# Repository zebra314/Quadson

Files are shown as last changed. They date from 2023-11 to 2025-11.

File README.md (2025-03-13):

# Quadson

## Description

## Usage

### Simulation

- Run the simulation

  ```sh
  make
  ```

- Use docker for simulation

  ```sh
  make SIM_METHOD=docker
  ```

### Real time control on Raspberry Pi

- Activate the robot

  ```sh
  make nav
  ```

- Clean the project

  ```sh
  make nav-clean
  ```

## Files

```sh
quadson_pi/
│
├── build/
│ ├── ...
│ .
│ .
│ .
│ └──
│
├── include/
│ ├── actuator.h
│ ├── AHRS.h
│ ├── can_interface.h
│ ├── can_protocol.h
│ ├── leg_group.h
│ ├── quadson.h
│ └── utility.h
│
├── library/
│ ├── ...
│ .
│ .
│ .
│ └──
│
├── source/
│ ├── actuator.cpp
│ ├── AHRS.cpp
│ ├── can_interface.cpp
│ ├── can_protocol.cpp
│ ├── leg_group.cpp
│ ├── main.cpp
│ └── quadson.cpp
│
├── python_scripts/
│ ├── CAN_MotorControl.py
│ └── quad_calc_test.py
│
├── start_can.sh
│
└── stop_can.sh
```

- `actuator.h/actuator.cpp`: Define the basic function for a single actuator, such as enable, disable, set angle, set omega, get information, etc.

- `AHRS.h/AHRS.cpp`: Define the basic function and algorithm for the Attitude and Heading Reference System (AHRS) module. It is used to get the orientation of the robot.

- `main.cpp`: Main file of the project

- `can_interface.h/can_interface.cpp`: Create a can interface class to communicate with the can bus from the computer to the robot.

  ```sh
  Actuator alpha ─┐
  Actuator beta  ───> CAN BUS <───> Raspberry Pi
  Actuator gamma ─┘
  ```

- `can_protocol.h/can_protocol.cpp`: Define the protocol to communicate with the can bus. It includes the message ID(standard or extended), the message type, the message data, etc.

- `leg_group.h/leg_group.cpp`: Define the leg group class to control the leg group of the robot. It unified three actuators and responsible for the inverse kinematics, forward kinematics, gait planning and pid control.

- `quadson.h/quadson.cpp`: Define the main class of the project. It includes the main loop of the robot, the initialization of the robot, it also unified the four leg groups and responsible for sending the command to the actuators via the can bus.

- `utility.h`: Define some utility functions

- `start_can.sh`: Bash script to start the can interface

- `stop_can.sh`: Bash script to stop the can interface

## References

- [Mahony AHRS algorithm implemented by Madgwick](http://x-io.co.uk/open-source-imu-and-ahrs-algorithms/)

  According to the Mahony AHRS algorithm implemented by Madgwick and adapted by Igor Vereninov, provided by Emlid Ltd (c) 2014:

  ```bibtex
  @MISC{madgwick2014,
  author =   {Madgwick, S. and Vereninov, I.},
  title =    {Mahony AHRS algorithm},
  howpublished = {\url{http://x-io.co.uk/open-source-imu-and-ahrs-algorithms/}},
  year = {2014}
  }
  ```

- [PyBullet](http://pybullet.org)

  ```bibtex
  @MISC{coumans2021,
  author =   {Erwin Coumans and Yunfei Bai},
  title =    {PyBullet, a Python module for physics simulation for games, robotics and machine learning},
  howpublished = {\url{http://pybullet.org}},
  year = {2016--2021}
  }
  ```

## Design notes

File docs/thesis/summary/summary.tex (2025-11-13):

\documentclass[a4paper,11pt]{article}
\usepackage[a4paper, margin=2.5cm]{geometry}
\usepackage[utf8]{inputenc}
\usepackage{graphicx}
\usepackage{caption}
\usepackage{subcaption}
\usepackage{float}
\usepackage{amsmath}
\usepackage{pgfplots}
\usepackage{ffcode}
\usepackage{booktabs}
\usepackage{xcolor}
\usepackage{listings}
\usepackage{array}
\usepackage{tikz}
\usepackage{algorithm}
\usepackage{algpseudocode}
\usetikzlibrary{calc,patterns,angles,quotes}

\pgfplotsset{compat=1.18} 

\makeatletter
\newenvironment{breakablealgorithm}
{% \begin{breakablealgorithm}
\begin{center} %
\refstepcounter{algorithm}% New algorithm
%\hrule height.8pt depth0pt \kern2pt% \@fs@pre for \@fs@ruled
\hrule height.8pt depth0pt \kern2pt% \@fs@pre for \@fs@ruled
\renewcommand{\caption}[2][\relax]{% Make a new \caption
{\raggedright\textbf{\ALG@name~\thealgorithm} ##2\par}
\ifx\relax##1\relax
\addcontentsline{loa}{algorithm}{\protect\numberline{\thealgorithm}##2}%
\else
\addcontentsline{loa}{algorithm}{\protect\numberline{\thealgorithm}##1}%
\fi
\kern2pt\hrule\kern2pt
}
}{% \end{breakablealgorithm}
\kern2pt\hrule\relax% \@fs@post for \@fs@ruled
\end{center} %
}
\makeatother

\begin{document}
	
\title{
	\textbf{Quadson: A Quadruped Robot Control Framework}
}
\author{Ying Pei Lin}
\date{Spring 2025}
\maketitle

\section{Introduction}

Quadson is a 3D printed quadruped robot designed as a platform for exploring advanced robotic motion and control.
This document includes its forward kinematics, inverse kinematics, differential kinematics and expands to body kinematics and locomotion.
Following the analysis, we will introduce the process of performing simultion in Pybullet and using deep
reinforcement learning to improve the robot's control and performance.

\section{Forward Kinematics}

For each leg of the robot, we define the reference frame with its origin at point $p_1$. 
Two motors are positioned at $p_1$ and $p_5$ respectively, and the third motor
connected to the entire leg assembly, controls the rotation around x axis. The remaining joints in the leg are all passive.

\begin{center}
\begin{tikzpicture}[scale=0.4]
	% Points
	\coordinate (p1) at (0,0);
	\coordinate (p2) at (-5.66,-5.66);
	\coordinate (p2_hori) at (-1.66,-5.66);
	\coordinate (p3) at (2.31,-11.70);
	\coordinate (pe) at (8.68,-16.54);
	\coordinate (p4) at (13.82,-5.66);
	\coordinate (p4_hori) at (17.82,-5.66);
	\coordinate (p5) at (8.16,0);
	\coordinate (p5_hori) at (12.16,0);

	% Lines
	\draw[thick] (p1) -- (p2) -- (p3) -- (p4) -- (p5) -- (p1);
	\draw[thick] (p3) -- (pe);
	\draw[dashed] (p2) -- (p2_hori);
	\draw[dashed] (p4) -- (p4_hori);
	\draw[dashed] (p5) -- (p5_hori);
	
	% Axis
	\draw[thick,->] (-5,0,0) -- (-3,0,0) node[right] {$x$};
	\draw[thick,->] (-5,0,0) -- (-5,2,0) node[above] {$y$};
	\draw[thick,->] (-5,0,0) -- (-5,0,2) node[left] {$z$};
	\draw[red,->] (-3.8,-0.2,-0.7) arc[start angle=0,end angle=270,radius=0.5cm] node[midway,above] {$\theta_0$};

	% Point tags
	\foreach \p in {p1, p2, pe, p4, p5} {
			\fill[black] (\p) circle (4pt);
			\node[above] at (\p) {\p};
	}
	\fill[black] (p3) circle (4pt);
	\node[below] at (p3) {p3};

	% Length tags
	\draw[blue, dashed] (p1) -- (p5) node[midway, above] {$L_{0}$};
	\draw[blue, dashed] (p1) -- (p2) node[midway, above] {$L_{1}$};
	\draw[blue, dashed] (p2) -- (p3) node[midway, below] {$L_{2}$};
	\draw[blue, dashed] (p3) -- (pe) node[midway, below] {$L_{3}$};
	\draw[blue, dashed] (p3) -- (p4) node[midway, below] {$L_{4}$};
	\draw[blue, dashed] (p4) -- (p5) node[midway, below] {$L_{5}$};

	% Angle tags
	\pic [draw=red, text=red, <-, "$\theta_1$", angle radius=0.7cm] {angle=p2--p1--p5};
	\pic [draw=red, text=red, <-, "$\theta_2$", angle radius=1.2cm] {angle=p3--p2--p2_hori};
	\pic [draw=red, text=red, <-, "$\theta_4$", angle radius=0.7cm] {angle=p3--p4--p4_hori};
	\pic [draw=red, text=red, <-, "$\theta_5$", angle radius=1cm] {angle=p4--p5--p5_hori};
\end{tikzpicture}
\end{center}

The following algorithm takes the angle of three motors as input and computes the position of the end-effector.

\begin{breakablealgorithm}
	\caption{Compute Leg End-Point}
	\begin{algorithmic}[1]
			\Require Motor angles $\theta_0, \theta_1, \theta_5$
			\State Compute initial 2D joint positions:
			\begin{align*}
				&p_2 = (L_1 \cos \theta_1, -L_1 \sin \theta_1), p_5 = (L_0, 0), \\
				&p_4 = p_5 + (L_5 \cos \theta_5, -L_5 \sin \theta_5)
			\end{align*}
			\State Compute distances:
			$$
					L_{14} = \| p_4 - p_1 \|, \quad
					L_{24} = \| p_4 - p_2 \|
			$$
			\State Solve for $p_3$ using angles:
			$$
					\theta_2 = \cos^{-1} \left( \frac{L_2^2 + L_{24}^2 - L_4^2}{2 L_2 L_{24}} \right) +
										 \cos^{-1} \left( \frac{L_1^2 + L_{24}^2 - L_{14}^2}{2 L_1 L_{24}} \right) - (\pi - \theta_1)
			$$
			$$
					p_3 = p_2 + L_2 (\cos \theta_2, -\sin \theta_2)
			$$
			\State Compute endpoint:
			$$
					p_e = p_2 + (L_2 + L_3)(\cos \theta_2, -\sin \theta_2)
			$$
			\State Transform to 3D using rotation matrix:
			$$
				R_{\theta_0} =
				\begin{bmatrix}
						1 & 0 & 0 \\
						0 & \cos(-\theta_0) & -\sin(-\theta_0) \\
						0 & \sin(-\theta_0) & \cos(-\theta_0)
				\end{bmatrix}, 
				p_e = R_{\theta_0} \times \begin{bmatrix} p_e[0] \\ p_e[1] \\ 0 \end{bmatrix}
			$$
			\State \Return $p_e$
	\end{algorithmic}
\end{breakablealgorithm}

\section{Inverse Kinematics}

In real world scenarios, controlling position of the end-effector to reach to a certain position
is often more pratical than setting the angles directly. For example, to move the end-effector along 
a defined trajectory, achieving this by manually adjusting the three motor angles is nearly impossible 
due to the complexity of the joint movements. 

Therefore we need the following algorithm 
to compute the angles of the motor corresponding to a given target position.

\begin{breakablealgorithm}
	\caption{Compute Joint Angles from End-Point}
	\begin{algorithmic}[1]
			\Require End-point position $(x, y, z)$
			\State Calculate angle of motor 0:
			$$
				\theta_0 = -\tan^{-1} \left( \frac{z}{-y} \right)
			$$
			\State Translate points from 3D to 2D using rotation matrix:
			$$
				R_{\theta_0} =
					\begin{bmatrix}
						1 & 0 & 0 \\
						0 & \cos(-\theta_0) & -\sin(-\theta_0) \\
						0 & \sin(-\theta_0) & \cos(-\theta_0)
					\end{bmatrix}
			$$
			$$
				\begin{bmatrix} x' \\ y' \\ z' \end{bmatrix} = R_{\theta_0} \times \begin{bmatrix} x \\ y \\ z \end{bmatrix}
			$$
			\State Calculate angle 1:
			$$
				L_{1e} = \| (x', y') \|, \quad
				\theta_{e15} = \tan^{-1} \left( \frac{-y'}{x'} \right)
			$$
			$$
				\theta_{e12} = \cos^{-1} \left( \frac{L_1^2 + L_{1e}^2 - (L_2 + L_3)^2}{2 L_1 L_{1e}} \right)
			$$
			$$
				\theta_1 = \theta_{e15} + \theta_{e12}
			$$
			\State Compute positions of joints:
			$$
				p_1 = (0, 0), \quad
				p_2 = (L_1 \cos \theta_1, -L_1 \sin \theta_1)
			$$
			$$
				p_3 = \frac{(pe_2d \cdot L_2) + (p_2 \cdot L_3)}{L_2 + L_3}, \quad
				p_5 = (L_0, 0)
			$$
			\State Calculate angle 5:
			$$
				\theta_{350} = \tan^{-1} \left( \frac{-p_3[1]}{L_0 - p_3[0]} \right)
			$$
			$$
				\theta_{354} = \cos^{-1} \left( \frac{L_{35}^2 + L_5^2 - L_4^2}{2 L_{35} L_5} \right), \quad
				L_{35} = \| p_3 - p_5 \|
			$$
			$$
				\theta_5 = \pi - (\theta_{350} + \theta_{354})
			$$
			\State \Return $(\theta_0, \theta_1, \theta_5)$
	\end{algorithmic}
\end{breakablealgorithm}

\section{Differential Kinematics}

To control a quadruped robot's leg smoothly, we employ differential kinematics, which provides the relation between joint angular velocities and linear velocity of the end-effector.

Given the motor angles $\boldsymbol{\theta} = [\theta_0, \theta_1, \theta_5]^T$ and their angular velocities $\dot{\boldsymbol{\theta}} = [\omega_0, \omega_1, \omega_5]^T$. 
The linear velocity of the end-effector $\mathbf{v} = [v_x, v_y, v_z]^T$ can be represented as following:

$$
\mathbf{v} = \mathbf{J}(\boldsymbol{\theta}) \cdot \dot{\boldsymbol{\theta}}
$$

Where $\mathbf{J}(\boldsymbol{\theta}) \in \mathbf{R}^{3 \times 3}$ is the Jacobian matrix. It is updated continuously as $\boldsymbol{\theta}$ 
changes during motion even if the given linear velocity remain the same.
Note that angular velocity of the end-effector ($\omega_x, \omega_y, \omega_z$) is ignored because the foot contact does not require rotational control in this context.

To find the inverse, the required motor angular velocities for a desired end-effector linear velocity can be represented as following:

$$
\dot{\boldsymbol{\theta}} = \mathbf{J}^{+}(\boldsymbol{\theta}) \cdot \mathbf{v}
$$

Where $\mathbf{J}^+$ is the Moore-Penrose pseudoinverse of $\mathbf{J}$.

\begin{algorithm}[H]
	\caption{Compute Joint Velocities from End-Effector Velocity}
	\begin{algorithmic}[1]
		\Require End-effector velocity $\mathbf{v} = [v_x, v_y, v_z]^T$
		\State Read current joint angles $\boldsymbol{\theta}$
		\State Compute forward kinematics to get $\mathbf{p} = f(\boldsymbol{\theta})$
		\State Compute numerical Jacobian $\mathbf{J} \in \mathbf{R}^{3 \times 3}$
		\State Compute pseudoinverse $\mathbf{J}^{+}$
		\State Compute $\dot{\boldsymbol{\theta}} = \mathbf{J}^{+} \cdot \mathbf{v}$
		\State \Return $\dot{\boldsymbol{\theta}}$
	\end{algorithmic}
\end{algorithm}

Due to the difficulty in deriving $\mathbf{J}(\boldsymbol{\theta})$ analytically, we use the numerical finite difference method:

$$
\mathbf{J}_{:,i} = \frac{f(\boldsymbol{\theta} + \delta \cdot \mathbf{e}_i) - f(\boldsymbol{\theta})}{\delta}
$$

Where $f(\boldsymbol{\theta})$ is the forward kinematics function, $\delta$ is a small perturbation and 
$\mathbf{e}_i$ is a unit vector along the $i$-th motor axis.

\section{Body Kinematics}

To control the body pose of the robot when the legs are in contact with the ground, we take
the positions of the end-effectors in the world frame and the orientation of the body as inputs.
The goal is to transform the end-effector positions from the world frame to the shoulder frame, which is necessary for
calculating the inverse kinematics of the legs.

The world frame, $\boldsymbol{W}$, is the global reference frame in which the robot operates. 
The body frame, $\boldsymbol{B}$, is defined as the frame attached to the robot's center, and 
the shoulder frame, $\boldsymbol{S}$, is defined as the local frame attached to each leg's joint 1.

Each coordinate transformation is represented using a 4x4 homogeneous transformation matrix, including a rotation matrix $\mathbf{R} \in \mathbf{R}^{3 \times 3}$
and a translation vector $\mathbf{p} \in \mathbf{R}^{3}$:

$$
T = \begin{bmatrix}
R & p \\
0 & 1
\end{bmatrix}
$$

The steps to compute the foot positions in the shoulder frame are as follows:

\begin{algorithm}[H]
\caption{Compute Foot Position in Shoulder Frame}
\begin{algorithmic}[1]
\Require end-effector positions $p^w_i$, body orientation $(roll, pitch, yaw)$
\State Compute body-to-world transform, $T_b$
\For{each leg $i$}
    \State Get shoulder-to-body transform $T_{s_i}^b$ (predefined by geometry)
    \State Compute shoulder-to-world transform, $T_{s_i} = T_b \cdot T_{s_i}^b$
    \State Compute world-to-shoulder transform, $T_w^{s_i} = T_{s_i}^{-1}$
    \State Project world foot point into shoulder frame:
    $$
    p_i^s = T_w^{s_i} p_i^w
    $$
\EndFor
\State \Return Foot positions $p_i^s$ in shoulder frames
\end{algorithmic}
\end{algorithm}

\section{Locomotion}

Locomotion control is crucial for quadruped robots to enable them to move efficiently. The motion of the robot depends on the type of gait used, and different gaits have different characteristics such as step height, length, and timing.

The following first algorithm computes the phases of each leg based on time. Once the phase of each leg is determined, the next step is to calculate the end-effector positions for each leg.
The second algorithm computes corresponding end-effector points. The position is calculated differently for the stance and swing phases of each gait cycle.

\begin{algorithm}[H]
	\caption{Locomotion Phase Calculation}
	\begin{algorithmic}[1]
		\Require Gait type: \texttt{gait\_type} ('walk', 'trot', 'pace', 'bound', or 'gallop')
		\State Calculate the current phase of each leg based on the current time:
		$$
			\text{cycle\_progress} = \frac{\text{time} \% \text{cycle\_time}}{\text{cycle\_time}}
		$$
		\For{each leg in the robot's leg configuration}
			\State Calculate phase based on cycle progress:
			$$
				\text{phase\_dict[leg\_name]} = (\text{cycle\_progress} + \text{phase\_offset}) \% 1.0
			$$
		\EndFor
		\State \Return \texttt{phase\_dict}
	\end{algorithmic}
\end{algorithm}

\begin{algorithm}[H]
	\caption{End-Effector Points Calculation}
	\begin{algorithmic}[1]
		\Require Current time: \texttt{time}
		\State Get current phase for each leg using \texttt{get\_current\_phase(time)}
		\For{each leg in the robot's leg configuration}
			\If{phase of the leg is in the stance phase (i.e., less than \texttt{duty\_factor})}
				\State Interpolate between the stance start and end points:
				\begin{align*}
					&\text{p\_start} = (start\_x, base\_y), \\
					&\text{p\_end} = (start\_x + \text{direction} \times \text{step\_length}, base\_y) \\
					&p = \text{p\_start} + (\text{p\_end} - \text{p\_start}) \times \frac{\text{phase}}{\text{duty\_factor}}
				\end{align*}
				\State Set \texttt{x, y} coordinates based on interpolation
			\Else
				\State Interpolate using cubic Bezier curve for swing phase:
				\begin{align*}
					&p_0 = (start\_x + direction \times \text{step\_length}, base\_y) \\
					&p_1 = (start\_x + direction \times \text{step\_length}/2, base\_y + \text{step\_height}) \\
					&p_2 = (start\_x, base\_y + \text{step\_height}/2), \quad p_3 = (start\_x, base\_y) \\
					&(x, y) = \text{cubic\_bezier}(t, p_0, p_1, p_2, p_3)
				\end{align*}
			\EndIf
			\State Set \texttt{ee\_points[leg\_name]} to the calculated coordinates
		\EndFor
		\State \Return end-effector points: \texttt{ee\_points}
	\end{algorithmic}
\end{algorithm}

Duty factor, the fraction of the cycle where the leg is in contact with the ground.

The cubic Bezier curve is used for the swing phase to smoothly interpolate the leg's motion. The following formula is used to calculate the position on the cubic Bezier curve.

\begin{algorithm}[H]
	\caption{Cubic Bezier Curve}
	\begin{algorithmic}[1]
		\Require Interpolation factor: \texttt{t}, Control points: \texttt{p0, p1, p2, p3}
		\State Define the control points as a matrix:
		$$
			\text{points} = \begin{bmatrix} p_0 \\ p_1 \\ p_2 \\ p_3 \end{bmatrix}
		$$
		\State Define the Bernstein coefficients for the cubic curve:
		$$
			\text{coeffs} = \begin{bmatrix} (1-t)^3 & 3(1-t)^2t & 3(1-t)t^2 & t^3 \end{bmatrix}
		$$
		\State Calculate the position on the curve:
		$$
			(x, y) = \text{coeffs} \times \text{points}
		$$
		\State \Return position \texttt{(x, y)}
	\end{algorithmic}
\end{algorithm}

\section{Simulation}

After implementing the algorithms, we first test them in python notebook.
We use \text{matplotlib} to visualize the robot's motion and check if the end-effector positions are correct.

\begin{figure}[H]
  \centering
	
  \caption{Visualized Body Inverse Kinematics}
  \label{fig:body}
\end{figure}

And for the differential kinematics, we compare the actual end-effector velocities with the desired velocities to ensure the control is accurate.
As shown in the figure below, the vector of actual end-effector velocity fits well with the desired velocity.

\begin{figure}[H]
  \centering
	
  \caption{Visualized Differential Kinematics}
  \label{fig:diff}
\end{figure}

Next, we move to the simulation in Pybullet.
Pybullet is a physics engine that allows us to simulate the robot's motion in a realistic environment.
We first use Blender and its extension, Phobos, to transform the solidwork model into a URDF file.
Then we load the URDF file into Pybullet and set up the simulation environment.

\begin{figure}[H]
  \centering
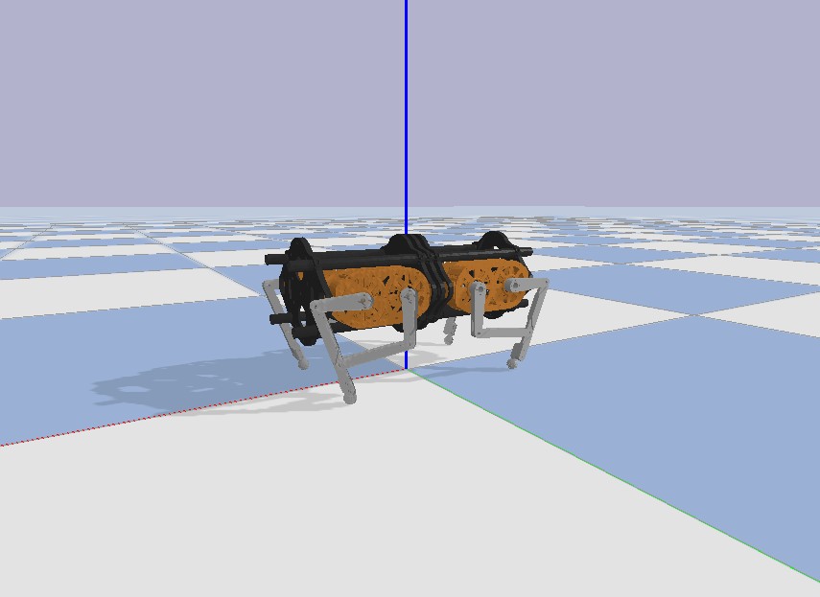
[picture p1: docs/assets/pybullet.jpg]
	
  \caption{Simulation in Pybullet}
  \label{fig:bullet}
\end{figure}

However, Pybullet does not support the closed chain mechanism of the robot. Therefore, we need to 
cut the each leg into two parts: the upper leg and the lower leg. Then, in the simulation, 
we use the kinematic algorithm to control the position of all links directly to simulate the
closed chain mechanism.

\section{Deep Reinforcement Learning}

To improve Quadson's locomotion stability, we apply deep reinforcement learning with PPO algorithm to generate adaptive offsets for the end-effector positions. This section includes the environment, RL formulation, and training process.

\subsection{Environment Setup}

We developed a custom Gymnasium environment, \texttt{QuadsonEnv}, using Pybullet for simulation. The environment includes:
\begin{itemize}
    \item \textbf{Physics}: Gravity at \(-9.81 \, \text{m/s}^2\), with a plane having friction (lateral: 0.8, spinning: 0.1, rolling: 0.01) and restitution (0.2).
    \item \textbf{Robot}: Quadson with 12 actuated joints, controlled via end-effector offsets.
    \item \textbf{Time Step}: \(1/240 \, \text{s}\) for stable simulation.
\end{itemize}

\subsection{RL Formulation}

The RL problem is defined as follows:

\begin{itemize}
    \item \textbf{Observation Space}: A 29-dimensional vector:
    \begin{itemize}
        \item Body state: roll, pitch, yaw, linear velocity (\(v_x, v_y, v_z\)), angular velocity (\(\omega_x, \omega_y, \omega_z\)) — 9 dimensions.
        \item Joint state: Positions of 12 joints.
        \item Leg phases: Sine and cosine of phases for four legs (LF, RF, LH, RH) — 8 dimensions.
    \end{itemize}
    \item \textbf{Action Space}: A 12-dimensional vector of end-effector offsets (\(x, y, z\) for each leg), bounded between \(-5\) and \(5\) cm.
    \item \textbf{Reward Function}: Combines multiple terms:
    \begin{align*}
			r = & \, 1.0 \cdot \exp(-0.5 (v_x - 0.5)^2) & \text{(forward velocity)} \\
					& - 0.8 \cdot (0.5 v_y^2 + 0.3 \omega_y^2) & \text{(lateral penalty)} \\
					& - 0.8 \cdot (0.5 v_z^2 + 0.3 \omega_z^2) & \text{(vertical penalty)} \\
					& - 1.0 \cdot (40 \text{roll}^2 + 30 \text{pitch}^2 + 5 \text{yaw}^2) & \text{(orientation penalty)} \\
					& - 0.5 \cdot \text{(additional terms for stability and efficiency)}.
    \end{align*}
    Key goals include maintaining forward speed (\(0.5 \, \text{m/s}\)), height (\(0.2 \, \text{m}\)), and reduce the body orientation change during moving.
    \item \textbf{Termination}: Episode ends if roll or pitch exceeds \(45^\circ\), height drops below \(0.1 \, \text{m}\), or 4500 steps are reached.
\end{itemize}

\subsection{System Design}

\begin{figure}[H]
  \centering
	
  \caption{System Block Diagram}
  \label{fig:system}
\end{figure}

\subsection{Training Process}

We use the Proximal Policy Optimization (PPO) algorithm from Stable Baselines3 due to its stability and sample efficiency.
Hyperparameters (e.g., learning rate, batch size) are under optimization during training.

\begin{figure}[H]
  \centering
	
  \caption{Reward}
  \label{fig:reward}
\end{figure}

\subsection{Results}

In the training, the agent performs 5000000 steps in total to interact with enviroment and update the network. 
Figure \ref{fig:compare_vel} shows that the forward velocity (vx) has increased, but it still not achieve the target velocity of 0.5m/s.
This could be due to limitations in the locomotion settings, where the model can only adjust the position of the end effector. To achieve the desired velocity, 
further tuning to the gait's length and timing is needed.

For vertical velocity (vz), both standard deviation and average have decreased slightly. Although the improvement is not significant but it still represents progress.
To further improve the stability, we may need to fine-tune the reward function or increase the depth of the deep network.

\begin{figure}[H]
	\centering
	\begin{subfigure}[b]{0.7\textwidth}
			\centering
			
			\caption{Locomotion Algorithm}
	\end{subfigure}
	\vfill
	\begin{subfigure}[b]{0.7\textwidth}
			\centering
			
			\caption{DRL Model}
	\end{subfigure}
	\caption{Velocity Comparison of Different Control Methods Over a 3-Second Trial.}
	\label{fig:compare_vel}
\end{figure}

Regarding the orientation stability, there's a significant improvement. As shown in Figure \ref{fig:compare_ori},
both the roll and pitch averages are now close to zero, with their standard deviations reduced by over 80\%.

\begin{figure}[H]
	\centering
	\begin{subfigure}[b]{\textwidth}
		\centering
		
		\caption{Locomotion Alogrithm}
	\end{subfigure}
	\vfill
	\begin{subfigure}[b]{\textwidth}
		\centering
		
		\caption{RL Model}
	\end{subfigure}
	\caption{Orientation Comparision of Different Control Method Over a 3-Second Trial.}
	\label{fig:compare_ori}
\end{figure}

\section{Future Work}

So far, we have implemented and valided kinematic algorithms, 
setting up a virtual environment for motion testing and reinforcement 
learning training. The Deep RL model aims to improve locomotion stability with 
adaptive gait offsets. The next steps are:

\begin{enumerate}
	\item \textbf{Simulation-to-Reality Transfer}: Deploy algorithms and model to the physical robot, deal with factors like friction and motor latency through tuning or domain randomization.
	\item \textbf{Walking Stability}: Refine RL policy to handle the movement in different terrians, such as slopes or uneven surfaces.
	\item \textbf{Sensor Integration}: Add IMU or LiDAR for real-time feedback and obstacle detection.
	\item \textbf{Expanded Locomotion}: Enable movement in various directions other than forward, such as sideways.
	\item \textbf{Recovery Mechanisms}: Enable self-righting or failure adaptation to protect the robot from falling.
	\item \textbf{Migrate to Isaac Gym}: Transition the simulation environment to Isaac Gym for better scalability and performance, using its advanced physics engine and GPU acceleration for more efficient training and testing.
\end{enumerate}

These steps will transition Quadson from simulation to a functional real-world robot.

\section{Conclusion}

We developed a kinematic framework for Quadson, covering forward, inverse, differential, and body kinematics, alongside locomotion control. These algorithms were validated in Pybullet, where simulations confirmed accurate end-effector positioning and velocity tracking. 
To enhance stability, we initiated deep reinforcement learning with PPO to adjust gait offsets, with training ongoing. Despite Pybullet's limitation with closed-chain mechanisms, we adapted by controlling link positions directly. This work establishes Quadson as a platform for robotic motion studies, 
blending classical kinematics with Deep RL. The next step is real-world deployment, building on this foundation to achieve practical functionality.

\newpage
\section*{Division of Work}

\renewcommand{\arraystretch}{1.8}
\begin{table}[h!]
\centering
\begin{tabular}{|l|p{8cm}|p{3cm}|}
\hline
\textbf{Name} & \textbf{Responsibilities} & \textbf{Signature} \\ 
\hline
\textbf{Ying-Pei Lin} & System Design, Kinematics Derivation, Locomotion Algorithm Design, Model Training & \\
\hline
\end{tabular}
\end{table}

\section*{Supervisor Signature}
\vspace{1cm}

\noindent
\textbf{Name:} \rule{10cm}{0.4pt}

\vspace{1cm}

\noindent
\textbf{Signature:} \rule{10cm}{0.4pt}

\vspace{1cm}

\noindent
\textbf{Date:} \rule{10cm}{0.4pt}

\end{document}

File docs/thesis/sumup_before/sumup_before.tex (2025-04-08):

\documentclass[a4paper,11pt]{article}

\usepackage[utf8]{inputenc}
\usepackage{graphicx}
\usepackage{caption}
\usepackage{subcaption}
\usepackage{float}
\usepackage{amsmath}
\usepackage{pgfplots}
\usepackage{ffcode}
\usepackage{booktabs}
\usepackage{listings}
\usepackage{xcolor}
\usepackage{listings}
\usepackage{array}
\usepackage{tikz}
\usepackage{algorithm}
\usepackage{algpseudocode}
\usetikzlibrary{calc,patterns,angles,quotes}

\pgfplotsset{compat=1.18} 

\begin{document}
	
\title{
	\textbf{Quadson}
}
\author{Ying Pei Lin}
\date{Spring 2025}
\maketitle

\section*{Introduction}

Quadson is a 3D printed quadruped robot designed as a platform for exploring advanced robotic motion and control.
This document includes its forward kinematics, inverse kinematics, differential kinematics and expands to body kinematics and locomotion.
Following these analysis, we will introduce the process of performing simultion in Pybullet and using deep
reinforcement learning to improve the robot's control and performance.

\section*{Forward Kinematics}

For each leg of the robot, we define the reference frame with its origin at point $p_1$. 
Two motors are positioned at $p_1$ and $p_5$ respectively, and the third motor
connected to the entire leg assembly, controls the rotation around x axis. The remaining joints in the leg are all passive.

\begin{center}
\begin{tikzpicture}[scale=0.4]
	% Points
	\coordinate (p1) at (0,0);
	\coordinate (p2) at (-5.66,-5.66);
	\coordinate (p2_hori) at (-1.66,-5.66);
	\coordinate (p3) at (2.31,-11.70);
	\coordinate (pe) at (8.68,-16.54);
	\coordinate (p4) at (13.82,-5.66);
	\coordinate (p4_hori) at (17.82,-5.66);
	\coordinate (p5) at (8.16,0);
	\coordinate (p5_hori) at (12.16,0);

	% Lines
	\draw[thick] (p1) -- (p2) -- (p3) -- (p4) -- (p5) -- (p1);
	\draw[thick] (p3) -- (pe);
	\draw[dashed] (p2) -- (p2_hori);
	\draw[dashed] (p4) -- (p4_hori);
	\draw[dashed] (p5) -- (p5_hori);
	
	% Axis
	\draw[thick,->] (-5,0,0) -- (-3,0,0) node[right] {$x$};
	\draw[thick,->] (-5,0,0) -- (-5,2,0) node[above] {$y$};
	\draw[thick,->] (-5,0,0) -- (-5,0,2) node[left] {$z$};
	\draw[red,->] (-3.8,-0.2,-0.7) arc[start angle=0,end angle=270,radius=0.5cm] node[midway,above] {$\theta_0$};

	% Point tags
	\foreach \p in {p1, p2, pe, p4, p5} {
			\fill[black] (\p) circle (4pt);
			\node[above] at (\p) {\p};
	}
	\fill[black] (p3) circle (4pt);
	\node[below] at (p3) {p3};

	% Length tags
	\draw[blue, dashed] (p1) -- (p5) node[midway, above] {$L_{0}$};
	\draw[blue, dashed] (p1) -- (p2) node[midway, above] {$L_{1}$};
	\draw[blue, dashed] (p2) -- (p3) node[midway, below] {$L_{2}$};
	\draw[blue, dashed] (p3) -- (pe) node[midway, below] {$L_{3}$};
	\draw[blue, dashed] (p3) -- (p4) node[midway, below] {$L_{4}$};
	\draw[blue, dashed] (p4) -- (p5) node[midway, below] {$L_{5}$};

	% Angle tags
	\pic [draw=red, text=red, <-, "$\theta_1$", angle radius=0.7cm] {angle=p2--p1--p5};
	\pic [draw=red, text=red, <-, "$\theta_2$", angle radius=1.2cm] {angle=p3--p2--p2_hori};
	\pic [draw=red, text=red, <-, "$\theta_4$", angle radius=0.7cm] {angle=p3--p4--p4_hori};
	\pic [draw=red, text=red, <-, "$\theta_5$", angle radius=1cm] {angle=p4--p5--p5_hori};
\end{tikzpicture}
\end{center}

The following algorithm takes the angle of three motors as input and computes the position of the end effector.
The process incorporates several safety check, prevent configurations that could potentially damage the mechanism.

\begin{algorithm}[H]
	\caption{Compute Leg End-Point}
	\begin{algorithmic}[1]
			\Require Motor angles $\theta_0, \theta_1, \theta_5$
			\State Compute initial 2D joint positions:
			\begin{align*}
				&p_2 = (L_1 \cos \theta_1, -L_1 \sin \theta_1), p_5 = (L_0, 0), \\
				&p_4 = p_5 + (L_5 \cos \theta_5, -L_5 \sin \theta_5)
			\end{align*}
			\State Compute distances:
			$$
					L_{14} = \| p_4 - p_1 \|, \quad
					L_{24} = \| p_4 - p_2 \|
			$$
			\State Solve for $p_3$ using angles:
			$$
					\theta_2 = \cos^{-1} \left( \frac{L_2^2 + L_{24}^2 - L_4^2}{2 L_2 L_{24}} \right) +
										 \cos^{-1} \left( \frac{L_1^2 + L_{24}^2 - L_{14}^2}{2 L_1 L_{24}} \right) - (\pi - \theta_1)
			$$
			$$
					p_3 = p_2 + L_2 (\cos \theta_2, -\sin \theta_2)
			$$
			\State Compute endpoint:
			$$
					p_e = p_2 + (L_2 + L_3)(\cos \theta_2, -\sin \theta_2)
			$$
			\State Transform to 3D using rotation matrix:
			$$
				R_{\theta_0} =
				\begin{bmatrix}
						1 & 0 & 0 \\
						0 & \cos(-\theta_0) & -\sin(-\theta_0) \\
						0 & \sin(-\theta_0) & \cos(-\theta_0)
				\end{bmatrix}, 
				p_e = R_{\theta_0} \times \begin{bmatrix} p_e[0] \\ p_e[1] \\ 0 \end{bmatrix}
			$$
			\State \Return $p_e$
	\end{algorithmic}
\end{algorithm}

\section*{Inverse Kinematics}

In real world scenarios, controlling position of the end effector to reach to a certain position
is often more pratical than setting the angles directly. For example, to move the end effector along 
a defined trajectory, achieving this by manually adjusting the three motor angles is nearly impossible 
due to the complexity of the joint movements. 

Therefore we need the following algorithm 
to compute the angles of the motor corresponding to a given target position.

\begin{algorithm}[H]
	\caption{Compute Joint Angles from End-Point}
	\begin{algorithmic}[1]
			\Require End-point position $(x, y, z)$
			\State Calculate angle of motor 0:
			$$
				\theta_0 = -\tan^{-1} \left( \frac{z}{-y} \right)
			$$
			\State Translate points from 3D to 2D using rotation matrix:
			$$
				R_{\theta_0} =
					\begin{bmatrix}
							1 & 0 & 0 \\
							0 & \cos(-\theta_0) & -\sin(-\theta_0) \\
							0 & \sin(-\theta_0) & \cos(-\theta_0)
					\end{bmatrix}
			$$
			$$
				\begin{bmatrix} x' \\ y' \\ z' \end{bmatrix} = R_{\theta_0} \times \begin{bmatrix} x \\ y \\ z \end{bmatrix}
			$$
			\State Calculate angle 1:
			$$
					L_{1e} = \| (x', y') \|, \quad
					\theta_{e15} = \tan^{-1} \left( \frac{-y'}{x'} \right)
			$$
			$$
					\theta_{e12} = \cos^{-1} \left( \frac{L_1^2 + L_{1e}^2 - (L_2 + L_3)^2}{2 L_1 L_{1e}} \right)
			$$
			$$
					\theta_1 = \theta_{e15} + \theta_{e12}
			$$
			\State Compute positions of joints:
			$$
					p_1 = (0, 0), \quad
					p_2 = (L_1 \cos \theta_1, -L_1 \sin \theta_1)
			$$
			$$
					p_3 = \frac{(pe_2d \cdot L_2) + (p_2 \cdot L_3)}{L_2 + L_3}, \quad
					p_5 = (L_0, 0)
			$$
			\State Calculate angle 5:
			$$
				\theta_{350} = \tan^{-1} \left( \frac{-p_3[1]}{L_0 - p_3[0]} \right)
			$$
			$$
					\theta_{354} = \cos^{-1} \left( \frac{L_{35}^2 + L_5^2 - L_4^2}{2 L_{35} L_5} \right), \quad
					L_{35} = \| p_3 - p_5 \|
			$$
			$$
					\theta_5 = \pi - (\theta_{350} + \theta_{354})
			$$
			\State \Return $(\theta_0, \theta_1, \theta_5)$
	\end{algorithmic}
\end{algorithm}

\section*{Differential Kinematics}

To control a quadruped robot's leg smoothly, we employ differential kinematics, which provides the relation between joint angular velocities and linear velocity of the end effector.

Given the motor angles $\boldsymbol{\theta} = [\theta_0, \theta_1, \theta_5]^T$ and their angular velocities $\dot{\boldsymbol{\theta}} = [\omega_0, \omega_1, \omega_5]^T$. 
The linear velocity of the end-effector $\mathbf{v} = [v_x, v_y, v_z]^T$ can be represented as following:

$$
\mathbf{v} = \mathbf{J}(\boldsymbol{\theta}) \cdot \dot{\boldsymbol{\theta}}
$$

Where $\mathbf{J}(\boldsymbol{\theta}) \in \mathbf{R}^{3 \times 3}$ is the Jacobian matrix. It is updated continuously as $\boldsymbol{\theta}$ 
changes during motion even if the given linear velocity remain the same.
Note that angular velocity of the end-effector ($\omega_x, \omega_y, \omega_z$) is ignored because the foot contact does not require rotational control in this context.

To find the inverse, the required motor angular velocities for a desired end-effector linear velocity:

$$
\dot{\boldsymbol{\theta}} = \mathbf{J}^{+}(\boldsymbol{\theta}) \cdot \mathbf{v}
$$

Where $\mathbf{J}^+$ is the Moore-Penrose pseudoinverse of $\mathbf{J}$.

\begin{algorithm}[H]
	\caption{Compute Joint Velocities from End-Effector Velocity}
	\begin{algorithmic}[1]
		\Require End-effector velocity $\mathbf{v} = [v_x, v_y, v_z]^T$
		\State Read current joint angles $\boldsymbol{\theta}$
		\State Compute forward kinematics to get $\mathbf{p} = f(\boldsymbol{\theta})$
		\State Compute numerical Jacobian $\mathbf{J} \in \mathbf{R}^{3 \times 3}$
		\State Compute pseudoinverse $\mathbf{J}^{+}$
		\State Compute $\dot{\boldsymbol{\theta}} = \mathbf{J}^{+} \cdot \mathbf{v}$
		\State \Return $\dot{\boldsymbol{\theta}}$
	\end{algorithmic}
\end{algorithm}

Due to the difficulty in deriving $\mathbf{J}(\boldsymbol{\theta})$ analytically, we use the numerical finite difference method:

$$
\mathbf{J}_{:,i} = \frac{f(\boldsymbol{\theta} + \delta \cdot \mathbf{e}_i) - f(\boldsymbol{\theta})}{\delta}
$$

Where $f(\boldsymbol{\theta})$ is the forward kinematics function, $\delta$ is a small perturbation and 
$\mathbf{e}_i$ is a unit vector along the $i$-th motor axis.

\section*{Body Kinematics}

To control the body pose of the robot when the legs are in contact with the ground, we take
the positions of the end-effectors in the world frame and the orientation of the body as inputs.
The goal is to transform the end-effector positions from the world frame to the shoulder frame, which is necessary for
calculating the inverse kinematics of the legs.

The world frame, $\boldsymbol{W}$, is the global reference frame in which the robot operates. 
The body frame, $\boldsymbol{B}$, is defined as the frame attached to the robot's center, and 
the shoulder frame, $\boldsymbol{S}$, is defined as the local frame attached to each leg's joint 1.

Each coordinate transformation is represented using a 4x4 homogeneous transformation matrix, including a rotation matrix $\mathbf{R} \in \mathbf{R}^{3 \times 3}$
and a translation vector $\mathbf{p} \in \mathbf{R}^{3}$:

$$
T = \begin{bmatrix}
R & p \\
0 & 1
\end{bmatrix}
$$

The steps to compute the foot positions in the shoulder frame are as follows:

\begin{algorithm}[H]
\caption{Compute Foot Position in Shoulder Frame}
\begin{algorithmic}[1]
\Require End effector positions $p^w_i$, body orientation $(roll, pitch, yaw)$
\State Compute body-to-world transform, $T_b$
\For{each leg $i$}
    \State Get shoulder-to-body transform $T_{s_i}^b$ (predefined by geometry)
    \State Compute shoulder-to-world transform, $T_{s_i} = T_b \cdot T_{s_i}^b$
    \State Compute world-to-shoulder transform, $T_w^{s_i} = T_{s_i}^{-1}$
    \State Project world foot point into shoulder frame:
    $$
    p_i^s = T_w^{s_i} p_i^w
    $$
\EndFor
\State \Return Foot positions $p_i^s$ in shoulder frames
\end{algorithmic}
\end{algorithm}

\section*{Locomotion}

Locomotion control is crucial for quadruped robots to enable them to move efficiently. The motion of the robot depends on the type of gait used, and different gaits have different characteristics such as step height, length, and timing.

The following first algorithm computes the phases of each leg based on time. Once the phase of each leg is determined, the next step is to calculate the end-effector positions for each leg.
The second algorithm computes corresponding end-effector points. The position is calculated differently for the stance and swing phases of each gait cycle.

\begin{algorithm}[H]
	\caption{Locomotion Phase Calculation}
	\begin{algorithmic}[1]
		\Require Gait type: \texttt{gait\_type} ('walk', 'trot', 'pace', 'bound', or 'gallop')
		\State Calculate the current phase of each leg based on the current time:
		$$
			\text{cycle\_progress} = \frac{\text{time} \% \text{cycle\_time}}{\text{cycle\_time}}
		$$
		\For{each leg in the robot's leg configuration}
			\State Calculate phase based on cycle progress:
			$$
				\text{phase\_dict[leg\_name]} = (\text{cycle\_progress} + \text{phase\_offset}) \% 1.0
			$$
		\EndFor
		\State \Return \texttt{phase\_dict}
	\end{algorithmic}
\end{algorithm}

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

The cubic Bezier curve is used for the swing phase to smoothly interpolate the leg's motion. The following formula is used to calculate the position on the cubic Bezier curve.

\begin{algorithm}[H]
	\caption{Cubic Bezier Curve}
	\begin{algorithmic}[1]
		\Require Interpolation factor: \texttt{t}, Control points: \texttt{p0, p1, p2, p3}
		\State Define the control points as a matrix:
		$$
			\text{points} = \begin{bmatrix} p_0 \\ p_1 \\ p_2 \\ p_3 \end{bmatrix}
		$$
		\State Define the Bernstein coefficients for the cubic curve:
		$$
			\text{coeffs} = \begin{bmatrix} (1-t)^3 & 3(1-t)^2t & 3(1-t)t^2 & t^3 \end{bmatrix}
		$$
		\State Calculate the position on the curve:
		$$
			(x, y) = \text{coeffs} \times \text{points}
		$$
		\State \Return position \texttt{(x, y)}
	\end{algorithmic}
\end{algorithm}

\section*{Simulation}

After implementing the algorithms, we first test them in python notebook.
We use \text{matplotlib} to visualize the robot's motion and check if the end-effector positions are correct.

\begin{figure}[H]
  \centering
	
  \caption{Visualized Body Inverse Kinematics}
  \label{fig:body}
\end{figure}

And for the differential kinematics, we compare the actual end-effector velocities with the desired velocities to ensure the control is accurate.
As shown in the figure below, the vector of actual end-effector velocity fits well with the desired velocity.

\begin{figure}[H]
  \centering
	
  \caption{Visualized Differential Kinematics}
  \label{fig:diff}
\end{figure}

Next, we move to the simulation in Pybullet.
Pybullet is a physics engine that allows us to simulate the robot's motion in a realistic environment.
We first use Blender and its extension, Phobos, to transform the solidwork model into a URDF file.
Then we load the URDF file into Pybullet and set up the simulation environment.

\begin{figure}[H]
  \centering
	
  \caption{Simulation in Pybullet}
  \label{fig:bullet}
\end{figure}

However, Pybullet does not support the closed chain mechanism of the robot. Therefore, we need to 
cut the each leg into two parts: the upper leg and the lower leg. Then, in the simulation, 
we use the kinematic algorithm to control the position of all links directly to simulate the
closed chain mechanism.

\section*{Deep Reinforcement Learning}

To enhance Quadson’s locomotion stability, we apply deep reinforcement learning (RL) to generate adaptive offsets for the end-effector positions. This section outlines the environment, RL formulation, and training process.

\subsection*{Environment Setup}

We developed a custom Gymnasium environment, \texttt{QuadsonEnv}, using Pybullet for simulation. The environment includes:
\begin{itemize}
    \item \textbf{Physics}: Gravity at \(-9.81 \, \text{m/s}^2\), with a plane having friction (lateral: 0.8, spinning: 0.1, rolling: 0.01) and restitution (0.2).
    \item \textbf{Robot}: Quadson with 12 actuated joints, controlled via end-effector offsets.
    \item \textbf{Time Step}: \(1/240 \, \text{s}\) for stable simulation.
\end{itemize}
The camera follows the robot at a fixed distance (0.8 m), yaw (75°), and pitch (\(-20^\circ\)).

\subsection*{RL Formulation}

The RL problem is defined as follows:

\begin{itemize}
    \item \textbf{Observation Space}: A 29-dimensional vector:
    \begin{itemize}
        \item Body state: roll, pitch, yaw, linear velocity (\(v_x, v_y, v_z\)), angular velocity (\(\omega_x, \omega_y, \omega_z\)) — 9 dimensions.
        \item Joint state: Positions of 12 joints.
        \item Leg phases: Sine and cosine of phases for four legs (LF, RF, LH, RH) — 8 dimensions.
    \end{itemize}
    \item \textbf{Action Space}: A 12-dimensional vector of end-effector offsets (\(x, y, z\) for each leg), bounded between \(-5\) and \(5\).
    \item \textbf{Reward Function}: Combines multiple terms:
    \begin{align*}
        r = & \, 1.0 \cdot \exp(-0.5 (v_x - 0.5)^2) & \text{(forward velocity)} \\
            & - 0.8 \cdot (0.5 v_y^2 + 0.3 \omega_y^2) & \text{(lateral penalty)} \\
            & - 0.8 \cdot (0.5 v_z^2 + 0.3 \omega_z^2) & \text{(vertical penalty)} \\
            & - 0.7 \cdot (1.7 \text{roll}^2 + 1.5 \text{pitch}^2 + 0.5 \text{yaw}^2) & \text{(orientation penalty)} \\
            & - 0.5 \cdot \text{(additional terms for stability and efficiency)}.
    \end{align*}
    Key goals include maintaining forward speed (\(0.5 \, \text{m/s}\)), height (\(0.2 \, \text{m}\)), and stability.
    \item \textbf{Termination}: Episode ends if roll or pitch exceeds \(45^\circ\), height drops below \(0.1 \, \text{m}\), or 4000 steps are reached.
\end{itemize}

\subsection*{Training Process}

We use the Proximal Policy Optimization (PPO) algorithm from Stable Baselines3 due to its stability and sample efficiency. Training occurs in Pybullet with:
\begin{itemize}
    \item \textbf{Callback}: A custom \texttt{PlottingCallback} tracks rewards, computes moving averages (window size: 25), and plots progress every episode.
    \item \textbf{Visualization}: Real-time plots of episode rewards, moving averages, and standard deviations saved as \texttt{rl\_training\_progress.pdf}.
\end{itemize}
Hyperparameters (e.g., learning rate, batch size) are under optimization during training.

\subsection*{Preliminary Results}

[Placeholder: Insert results here once training completes.]  
Training is ongoing. Initial observations suggest the agent learns to stabilize Quadson's gait. Final results will include average reward, stability metrics, and locomotion performance.

\section*{Future Work}

So far, we have implemented and valided kinematic algorithms, 
setting up a virtual environment for motion testing and reinforcement 
learning training. The RL model aims to improve locomotion stability with 
adaptive gait offsets. The next steps are:

\begin{enumerate}
	\item \textbf{Simulation-to-Reality Transfer}: Deploy algorithms and RL model to the physical robot, deal with factors like friction and motor latency through tuning or domain randomization.
	\item \textbf{Walking Stability}: Refine RL policy to handle the movement in different terrians, such as slopes or uneven surfaces.
	\item \textbf{Sensor Integration}: Add IMU or LiDAR for real-time feedback and obstacle detection.
	\item \textbf{Expanded Locomotion}: Enable movement in various directions other than forward, such as sideways.
	\item \textbf{Recovery Mechanisms}: Enable self-righting or failure adaptation to protect the robot from falling.
\end{enumerate}

These steps will transition Quadson from simulation to a functional real-world robot.

\section*{Conclusion}

We developed a kinematic framework for Quadson, covering forward, inverse, differential, and body kinematics, alongside locomotion control. These algorithms were validated in Pybullet, where simulations confirmed accurate end-effector positioning and velocity tracking. 
To enhance stability, we initiated deep reinforcement learning (RL) with PPO to adjust gait offsets, with training ongoing. Despite Pybullet's limitation with closed-chain mechanisms, we adapted by controlling link positions directly. This work establishes Quadson as a platform for robotic motion studies, 
blending classical kinematics with RL. The next step is real-world deployment, building on this foundation to achieve practical functionality.

\end{document}

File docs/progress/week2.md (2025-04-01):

# Progress Log

## Week (4/1-4/7)

### Done

- Summary the current progress in latex document
- Adjust training parameters

### Learnings

### Problems

### Next

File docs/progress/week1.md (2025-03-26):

# Progress Log

## Week 1 （2025-03-24 ~ 03-31）

### Done

- Create interface class for quadson
- Implement body kinematics in bullet
- Correct leg kinematics
- Implement gait class

### Learnings

### Problems

- In leg kinematics, the angles value calculated by set_motor_angles() and set_ee_point() are different.

### Next

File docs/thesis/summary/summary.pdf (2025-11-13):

## Quadson: A Quadruped Robot Control Framework

Ying Pei Lin

Spring 2025

## 1 Introduction

Quadson is a 3D printed quadruped robot designed as a platform for exploring advanced robotic motion and control. This document includes its forward kinematics, inverse kinematics, differential kinematics and expands to body kinematics and locomotion. Following the analysis, we will introduce the process of performing simultion in Pybullet and using deep reinforcement learning to improve the robot’s control and performance.

## 2 Forward Kinematics

For each leg of the robot, we define the reference frame with its origin at point p1. Two motors are positioned at p1 and p5 respectively, and the third motor connected to the entire leg assembly, controls the rotation around x axis. The remaining joints in the leg are all passive.

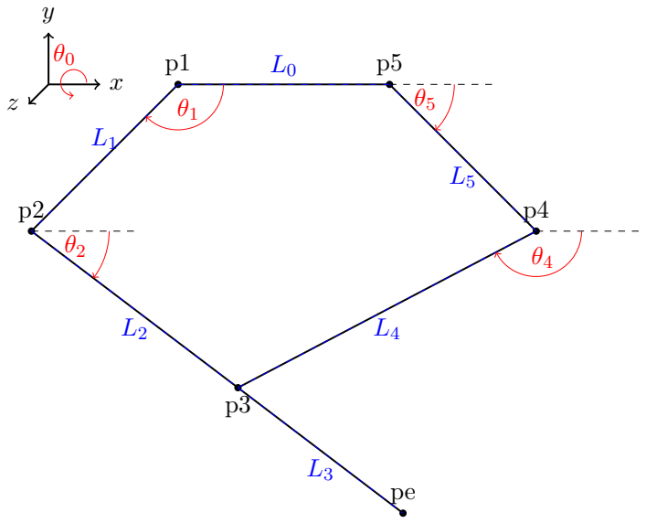
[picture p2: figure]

The following algorithm takes the angle of three motors as input and computes the position of the end-effector.

Algorithm 1 Compute Leg End-Point
Require: Motor angles θ0, θ1, θ5
1: Compute initial 2D joint positions:

p2 = (L1 cos θ1, −L1 sin θ1), p5 = (L0, 0), p4 = p5 + (L5 cos θ5, −L5 sin θ5)

2: Compute distances:
L14 = ∥p4 − p1∥, L24 = ∥p4 − p2∥

3: Solve for p3 using angles:

θ2 = cos⁻¹

L

2
2 + L

2
24 − L

2
4

2L2L24
+ cos⁻¹
L

2
1 + L

2
24 − L

2
14

2L1L24
− (π − θ1)

p3 = p2 + L2(cos θ2, − sin θ2)

4: Compute endpoint:
pe = p2 + (L2 + L3)(cos θ2, − sin θ2)

5: Transform to 3D using rotation matrix:

Rθ0 =

1 | 0 | 0
0 cos(−θ0) − sin(−θ0)
0 sin(−θ0) cos(−θ0)
- , pe = Rθ0 ×

pe[0]
pe[1]
0

6: return pe

## 3 Inverse Kinematics

In real world scenarios, controlling position of the end-effector to reach to a certain position is often more pratical than setting the angles directly. For example, to move the end-effector along a defined trajectory, achieving this by manually adjusting the three motor angles is nearly impossible due to the complexity of the joint movements.
Therefore we need the following algorithm to compute the angles of the motor corresponding to a given target position.

Algorithm 2 Compute Joint Angles from End-Point
Require: End-point position (x, y, z)
1: Calculate angle of motor 0:
| | θ0 = − tan⁻¹
z
−y

2: Translate points from 3D to 2D using rotation matrix:

Rθ0 =

1 | 0 | 0
0 cos(−θ0) − sin(−θ0)
0 sin(−θ0) cos(−θ0)

x

′
y

′
z

′

| = Rθ0 ×

x
y
z

3: Calculate angle 1:

L1e = ∥(x

′

, y′

)∥, θe15 = tan⁻¹

−y

′

x

′

θe12 = cos⁻¹

L

2
1 + L

2
1e − (L2 + L3)

2

2L1L1e

θ1 = θe15 + θe12

4: Compute positions of joints:

p1 = (0, 0), p2 = (L1 cos θ1, −L1 sin θ1)

p3 =

(pe2d · L2) + (p2 · L3)
L2 + L3

, p5 = (L0, 0)

5: Calculate angle 5:
θ350 = tan⁻¹
−p3[1]

L0 − p3[0]

θ354 = cos⁻¹

L

2
35 + L

2
5 − L

2
4
2L35L5
, L35 = ∥p3 − p5∥

θ5 = π − (θ350 + θ354)

6: return (θ0, θ1, θ5)

## 4 Differential Kinematics

To control a quadruped robot’s leg smoothly, we employ differential kinematics, which provides the relation between joint angular velocities and linear velocity of the end-effector.
Given the motor angles θ = [θ0, θ1, θ5]

T and their angular velocities θ˙ = [ω0, ω1, ω5]
T
. The
linear velocity of the end-effector v = [vx, vy, vz]

T
can be represented as following:

v = J(θ) · θ˙

Where J(θ) ∈ R³×3
is the Jacobian matrix. It is updated continuously as θ changes during motion even if the given linear velocity remain the same. Note that angular velocity of the end-effector (ωx, ωy, ωz) is ignored because the foot contact does not require rotational control in this context.
To find the inverse, the required motor angular velocities for a desired end-effector linear velocity can be represented as following:

θ˙ = J
+(θ) · v

Where J

+ is the Moore-Penrose pseudoinverse of J.

Algorithm 3 Compute Joint Velocities from End-Effector Velocity

Require: End-effector velocity v = [vx, vy, vz]

T
1: Read current joint angles θ
2: Compute forward kinematics to get p = f(θ) 3: Compute numerical Jacobian J ∈ R³×3
4: Compute pseudoinverse J

+
5: Compute θ˙ = J
+ · v
6: return θ˙

Due to the difficulty in deriving J(θ) analytically, we use the numerical finite difference method:

J:,i =

f(θ + δ · ei) − f(θ)
δ
Where f(θ) is the forward kinematics function, δ is a small perturbation and ei is a unit
vector along the i-th motor axis.

## 5 Body Kinematics

To control the body pose of the robot when the legs are in contact with the ground, we take the positions of the end-effectors in the world frame and the orientation of the body as inputs. The goal is to transform the end-effector positions from the world frame to the shoulder frame, which is necessary for calculating the inverse kinematics of the legs.

The world frame, W, is the global reference frame in which the robot operates. The body frame, B, is defined as the frame attached to the robot’s center, and the shoulder frame, S, is defined as the local frame attached to each leg’s joint 1.
Each coordinate transformation is represented using a 4x4 homogeneous transformation matrix, including a rotation matrix R ∈ R³×3 and a translation vector p ∈ R³
:

T =

R p

0 1

The steps to compute the foot positions in the shoulder frame are as follows:

Algorithm 4 Compute Foot Position in Shoulder Frame

Require: end-effector positions p

w
i

, body orientation (roll, pitch, yaw) 1: Compute body-to-world transform, Tb
2: for each leg i do
3: | Get shoulder-to-body transform T b si (predefined by geometry)
4: | Compute shoulder-to-world transform, Tsi = Tb · T

b
| si
5: | Compute world-to-shoulder transform, T si w = T −1 si
6: | Project world foot point into shoulder frame:
| p s i = T si w p w i

7: end for
8: return Foot positions p
| s i in shoulder frames

## 6 Locomotion

Locomotion control is crucial for quadruped robots to enable them to move efficiently. The motion of the robot depends on the type of gait used, and different gaits have different charac-teristics such as step height, length, and timing.
| The following first algorithm computes the phases of each leg based on time. Once the phase
of each leg is determined, the next step is to calculate the end-effector positions for each leg. The second algorithm computes corresponding end-effector points. The position is calculated differently for the stance and swing phases of each gait cycle.

Algorithm 5 Locomotion Phase Calculation
Require: Gait type: gait type (’walk’, ’trot’, ’pace’, ’bound’, or ’gallop’) 1: Calculate the current phase of each leg based on the current time:
| cycle progress = time%cycle time
| cycle time

2: for each leg in the robot’s leg configuration do
3: | Calculate phase based on cycle progress:
| phase dict[leg name] = (cycle progress + phase offset)%1.0

4: end for
5: return phase dict

Algorithm 6 End-Effector Points Calculation
Require: Current time: time
1: Get current phase for each leg using get current phase(time)
2: for each leg in the robot’s leg configuration do
3: | if phase of the leg is in the stance phase (i.e., less than duty factor) then
4: | Interpolate between the stance start and end points:

p start = (start x, base y),
p end = (start x + direction × step length, base y)

p = p start + (p end − p start) ×

phase
duty factor
5: | Set x, y coordinates based on interpolation
6: | else
7: | Interpolate using cubic Bezier curve for swing phase:

p0 = (start x + direction × step length, base y)
p1 = (start x + direction × step length/2, base y + step height) p2 = (start x, base y + step height/2), p3 = (start x, base y) (x, y) = cubic bezier(t, p0, p1, p2, p3)
8: | end if
9: | Set ee points[leg name] to the calculated coordinates
10: end for
11: return end-effector points: ee points

Duty factor, the fraction of the cycle where the leg is in contact with the ground.
The cubic Bezier curve is used for the swing phase to smoothly interpolate the leg’s motion. The following formula is used to calculate the position on the cubic Bezier curve.

Algorithm 7 Cubic Bezier Curve
Require: Interpolation factor: t, Control points: p0, p1, p2, p3
1: Define the control points as a matrix:

points =

p0
p1
p2
p3

2: Define the Bernstein coefficients for the cubic curve:

coeffs = -(1 − t)

3 3(1 − t)

2
t 3(1 − t)t

2
t

3

3: Calculate the position on the curve:

(x, y) = coeffs × points

4: return position (x, y)

## 7 Simulation

After implementing the algorithms, we first test them in python notebook. We use matplotlib to visualize the robot’s motion and check if the end-effector positions are correct.

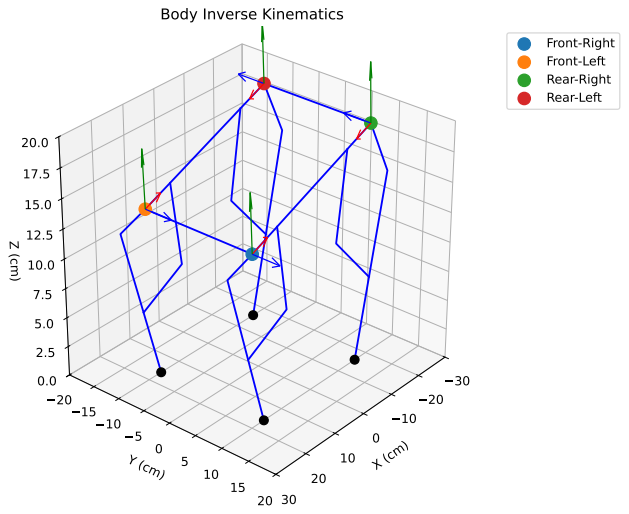
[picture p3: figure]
Body Inverse Kinematics; Front-Right Front-Left Rear-Right Rear-Left

Figure 1: Visualized Body Inverse Kinematics

And for the differential kinematics, we compare the actual end-effector velocities with the desired velocities to ensure the control is accurate. As shown in the figure below, the vector of actual end-effector velocity fits well with the desired velocity.

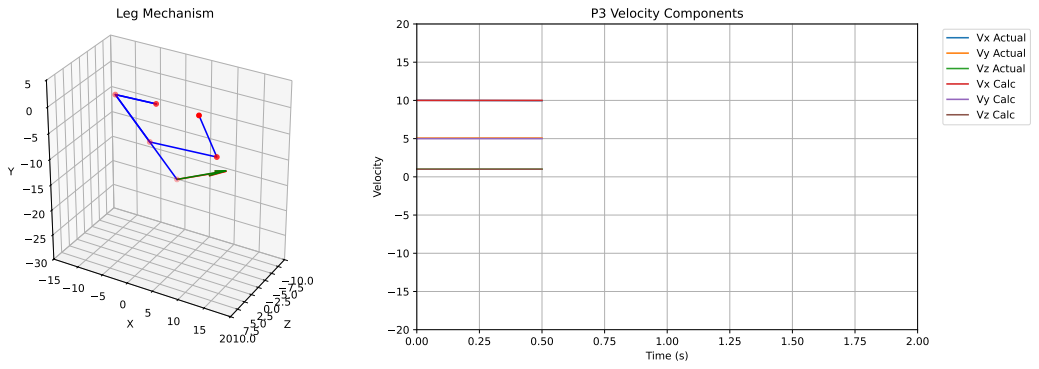
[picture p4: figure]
Leg Mechanism; Time (s); Velocity; P3 Velocity Components; Vx Actual; Vy Actual; Vz Actual; Vx Calc; Vy Calc; Vz Calc

Figure 2: Visualized Differential Kinematics

Next, we move to the simulation in Pybullet. Pybullet is a physics engine that allows us to simulate the robot’s motion in a realistic environment. We first use Blender and its extension, Phobos, to transform the solidwork model into a URDF file. Then we load the URDF file into Pybullet and set up the simulation environment.


Figure 3: Simulation in Pybullet

However, Pybullet does not support the closed chain mechanism of the robot. Therefore, we need to cut the each leg into two parts: the upper leg and the lower leg. Then, in the simulation, we use the kinematic algorithm to control the position of all links directly to simulate the closed chain mechanism.

## 8 Deep Reinforcement Learning

To improve Quadson’s locomotion stability, we apply deep reinforcement learning with PPO algorithm to generate adaptive offsets for the end-effector positions. This section includes the environment, RL formulation, and training process.

### 8.1 Environment Setup

We developed a custom Gymnasium environment, QuadsonEnv, using Pybullet for simulation. The environment includes:

- Physics: Gravity at −9.81 m/s²
, with a plane having friction (lateral: 0.8, spinning: 0.1, rolling: 0.01) and restitution (0.2).
- Robot: Quadson with 12 actuated joints, controlled via end-effector offsets.
- Time Step: 1/240 s for stable simulation.

### 8.2 RL Formulation

The RL problem is defined as follows:

- Observation Space: A 29-dimensional vector:

– Body state: roll, pitch, yaw, linear velocity (vx, vy, vz), angular velocity (ωx, ωy, ωz) — 9 dimensions.

– Joint state: Positions of 12 joints.

– Leg phases: Sine and cosine of phases for four legs (LF, RF, LH, RH) — 8 dimensions.

- Action Space: A 12-dimensional vector of end-effector offsets (x, y, z for each leg), bounded between −5 and 5 cm.

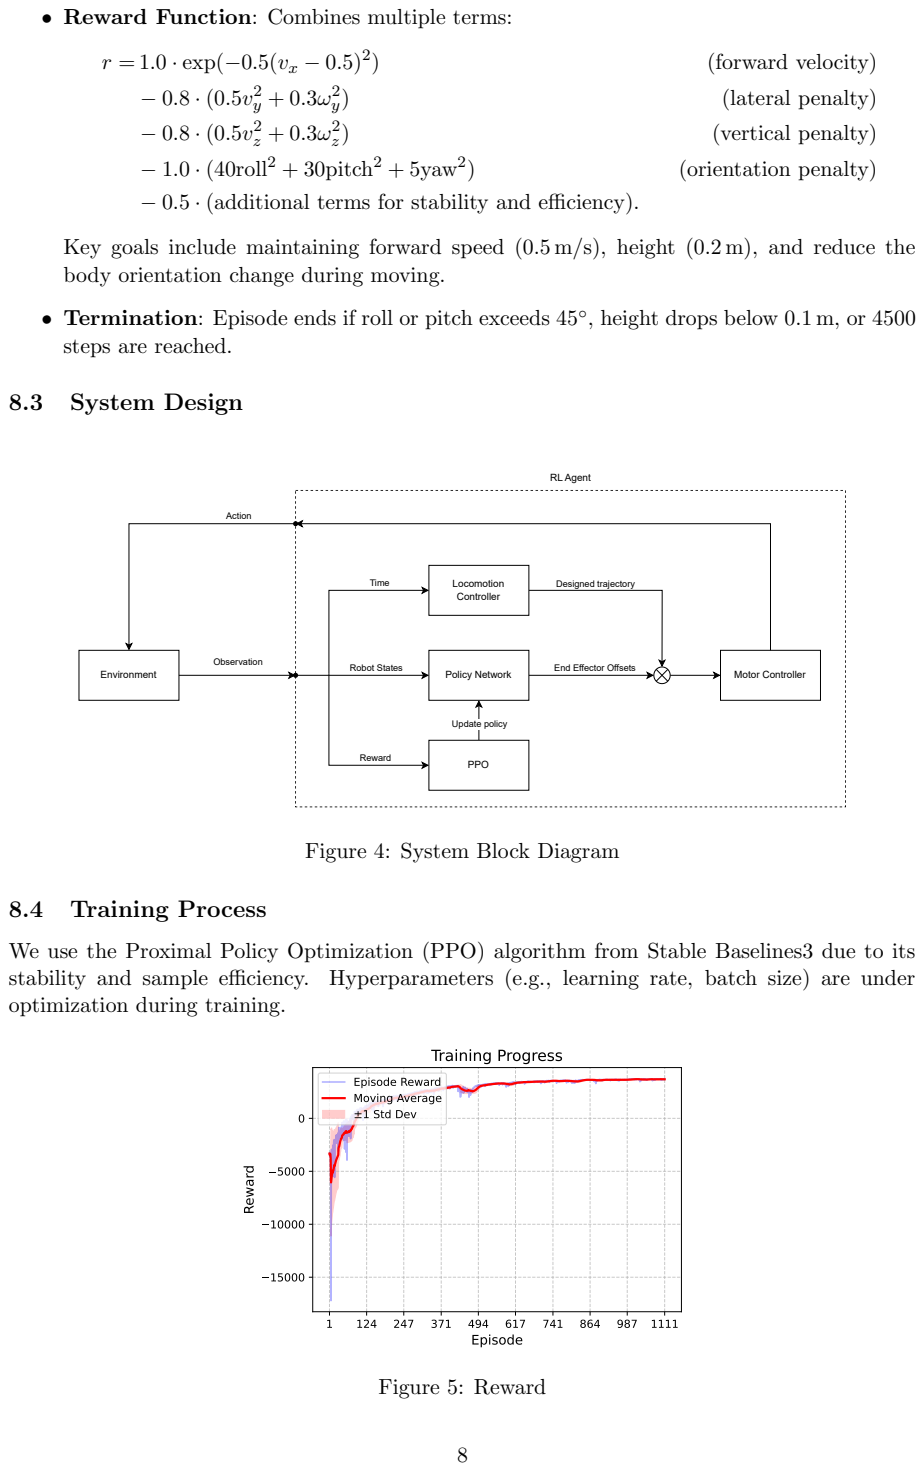
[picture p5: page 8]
r = 1.0 · exp(−0.5(vx − 0.5)²; (forward velocity); (lateral penalty); (vertical penalty); − 1.0 · (40roll² + 30pitch² + 5yaw²; (orientation penalty); 8.3 System Design; Locomotion; Designed trajectory; Controller; Action; Motor Controller; Reward; Environment; Update policy; PPO; Policy Network; Time; Observation; Robot States; RL Agent; 8.4 Training Process; Episode; Training Progress; Episode Reward; Moving Average; ±1 Std Dev; Figure 5: Reward

• Reward Function: Combines multiple terms:

− 0.5 · (additional terms for stability and efficiency).

Key goals include maintaining forward speed (0.5 m/s), height (0.2 m), and reduce the
body orientation change during moving.

• Termination: Episode ends if roll or pitch exceeds 45◦
steps are reached.

, height drops below 0.1 m, or 4500

End Effector Offsets

Figure 4: System Block Diagram

We use the Proximal Policy Optimization (PPO) algorithm from Stable Baselines3 due to its
stability and sample efficiency. Hyperparameters (e.g., learning rate, batch size) are under
optimization during training.

### 8.5 Results

In the training, the agent performs 5000000 steps in total to interact with enviroment and update the network. Figure 6 shows that the forward velocity (vx) has increased, but it still not achieve the target velocity of 0.5m/s. This could be due to limitations in the locomotion settings, where the model can only adjust the position of the end effector. To achieve the desired velocity, further tuning to the gait’s length and timing is needed.
For vertical velocity (vz), both standard deviation and average have decreased slightly. Al-though the improvement is not significant but it still represents progress. To further improve the stability, we may need to fine-tune the reward function or increase the depth of the deep network.

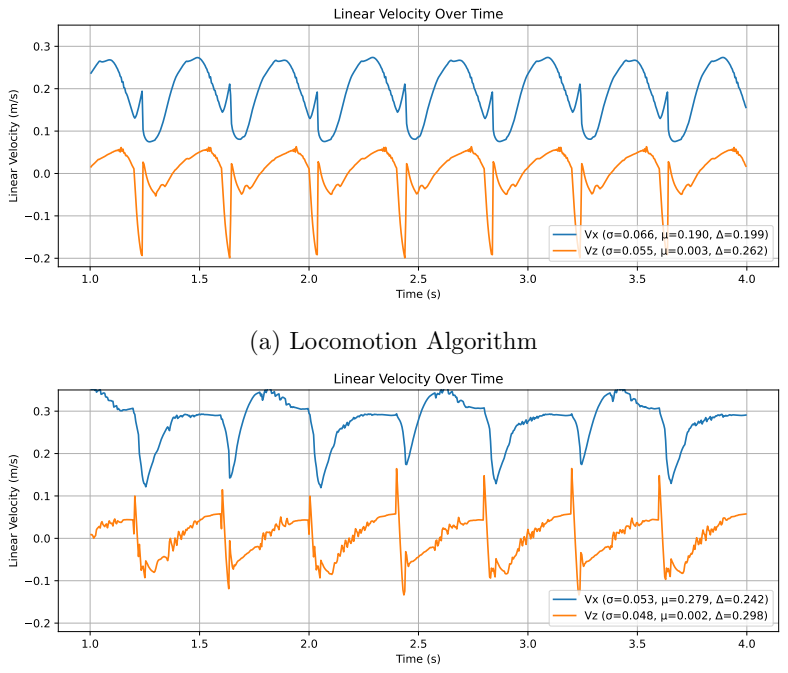
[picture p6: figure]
Time (s); Linear Velocity (m/s); Linear Velocity Over Time; (a) Locomotion Algorithm

(b) DRL Model

Figure 6: Velocity Comparison of Different Control Methods Over a 3-Second Trial.

Regarding the orientation stability, there’s a significant improvement. As shown in Figure 7, both the roll and pitch averages are now close to zero, with their standard deviations reduced by over 80%.

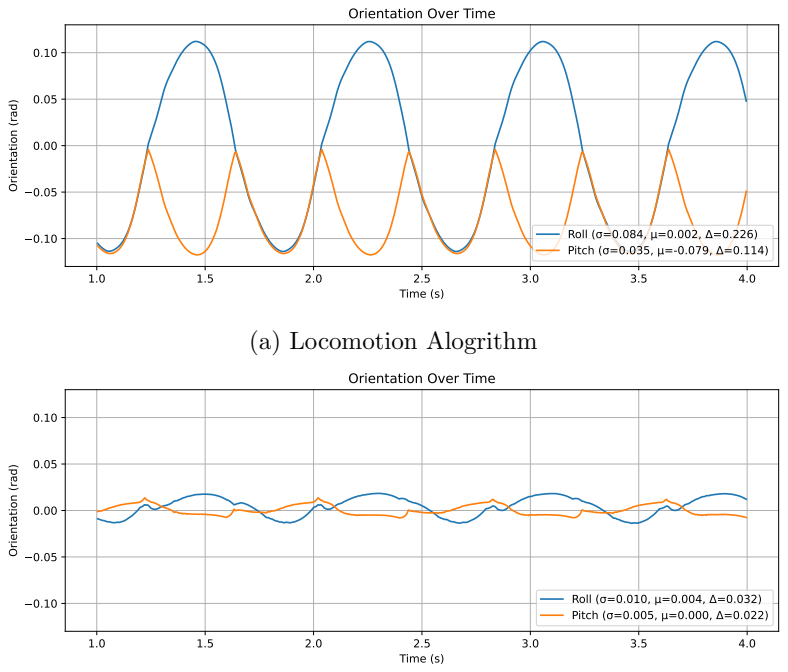
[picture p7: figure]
Time (s); Orientation (rad); Orientation Over Time; Roll ( =0.084, =0.002, =0.226) Pitch ( =0.035, =-0.079, =0.114); (a) Locomotion Alogrithm; Roll ( =0.010, =0.004, =0.032) Pitch ( =0.005, =0.000, =0.022)

(b) RL Model

Figure 7: Orientation Comparision of Different Control Method Over a 3-Second Trial.

## 9 Future Work

So far, we have implemented and valided kinematic algorithms, setting up a virtual environment for motion testing and reinforcement learning training. The Deep RL model aims to improve locomotion stability with adaptive gait offsets. The next steps are:

1. Simulation-to-Reality Transfer: Deploy algorithms and model to the physical robot, deal with factors like friction and motor latency through tuning or domain randomization.
2. Walking Stability: Refine RL policy to handle the movement in different terrians, such as slopes or uneven surfaces.
3. Sensor Integration: Add IMU or LiDAR for real-time feedback and obstacle detection.
4. Expanded Locomotion: Enable movement in various directions other than forward, such as sideways.
5. Recovery Mechanisms: Enable self-righting or failure adaptation to protect the robot from falling.
6. Migrate to Isaac Gym: Transition the simulation environment to Isaac Gym for better scalability and performance, using its advanced physics engine and GPU acceleration for more efficient training and testing.

These steps will transition Quadson from simulation to a functional real-world robot.

## 10 Conclusion

We developed a kinematic framework for Quadson, covering forward, inverse, differential, and body kinematics, alongside locomotion control. These algorithms were validated in Pybullet, where simulations confirmed accurate end-effector positioning and velocity tracking. To enhance stability, we initiated deep reinforcement learning with PPO to adjust gait offsets, with training ongoing. Despite Pybullet’s limitation with closed-chain mechanisms, we adapted by controlling link positions directly. This work establishes Quadson as a platform for robotic motion studies, blending classical kinematics with Deep RL. The next step is real-world deployment, building on this foundation to achieve practical functionality.

## Division of Work

Name | Responsibilities | Signature
Ying-Pei Lin | System Design, Kinematics Derivation, Loco-motion Algorithm Design, Model Training

## Supervisor Signature

Name:

Signature:

Date:

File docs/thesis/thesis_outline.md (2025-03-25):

# Thesis Outline

## 1. Introduction
- 動機：四足機器狗控制的困難（高維、延遲、不穩）
- 問題定義：在模擬中訓練可靠的步態策略，並能轉移至實體
- 貢獻摘要：
  - PPO 實作與實驗設計
  - 將策略轉換至 SAC 並比較效果
  - 探討 Domain Randomization 成效與策略穩定性
  - 模擬到實體之間的微調方法探索

## 2. Related Work
- PPO / SAC 在機器人控制上的應用
- Domain Randomization 技術
- Sim-to-Real transfer 的關鍵挑戰與方法
- 四足機器人相關控制方法

## 3. Methodology
- 模型與環境設定（PyBullet 模型、地形、初始姿態）
- PPO/SAC 訓練設定（reward、state space、action space）
- Domain Randomization 設計（哪些參數、分布範圍）
- 微調策略（如 fine-tuning、Residual Policy Learning）

## 4. Experiments
- 訓練步態與收斂結果分析
- PPO vs SAC 比較（reward 收斂、穩定性）
- 有無 Domain Randomization 的影響
- 測試 Transfer 成功率與失敗原因
- 消融實驗（不加某些隨機化或 reward 設定）

## 5. Discussion
- 學到什麼？哪些部分效果好/壞？為什麼？
- 討論 sim-to-real 的 gap 有哪些可以改善的方向

## 6. Conclusion & Future Work
- 總結貢獻與結果
- 下一步（硬體實測、自適應策略、更強的演算法）

---

## 附錄
- 模型細節、超參數表、訓練時間、硬體配置

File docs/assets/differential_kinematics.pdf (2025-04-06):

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

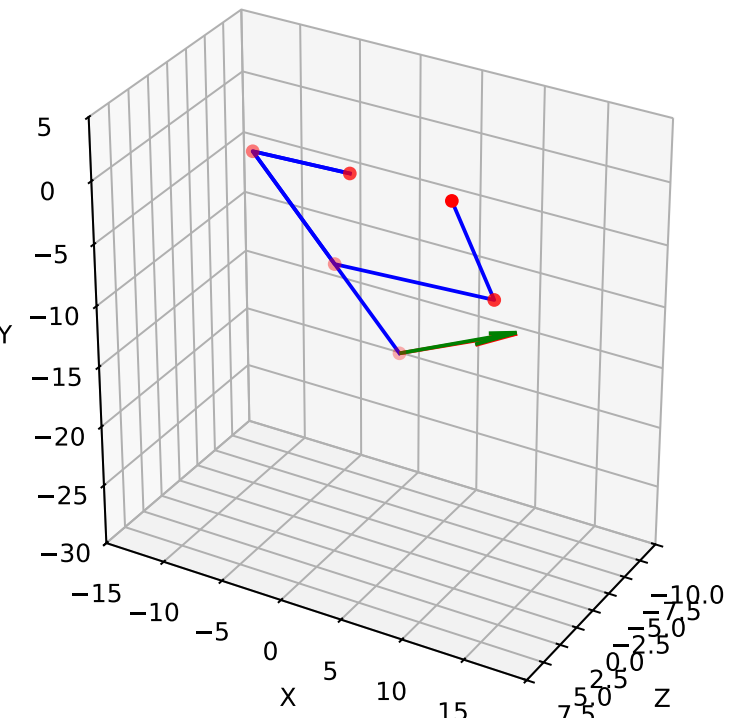
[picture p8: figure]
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

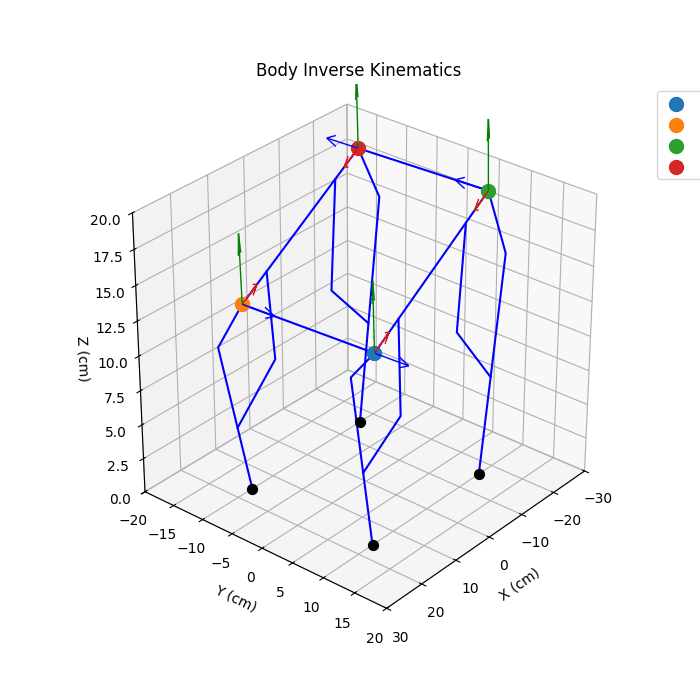
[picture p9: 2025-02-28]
docs/assets/quad_animation.gif

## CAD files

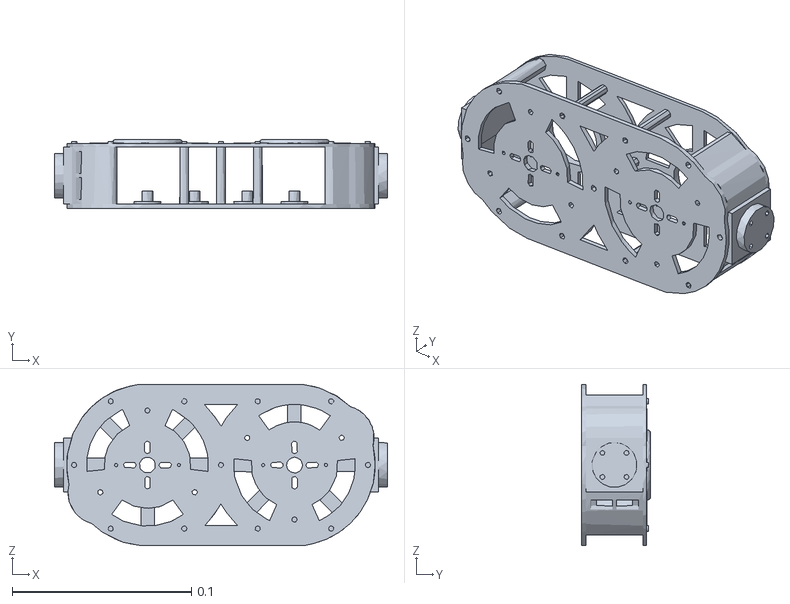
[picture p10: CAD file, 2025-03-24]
quadson_py/assets/single_leg/meshes/stl/link0.stl
0.186 x 0.0387 x 0.0901

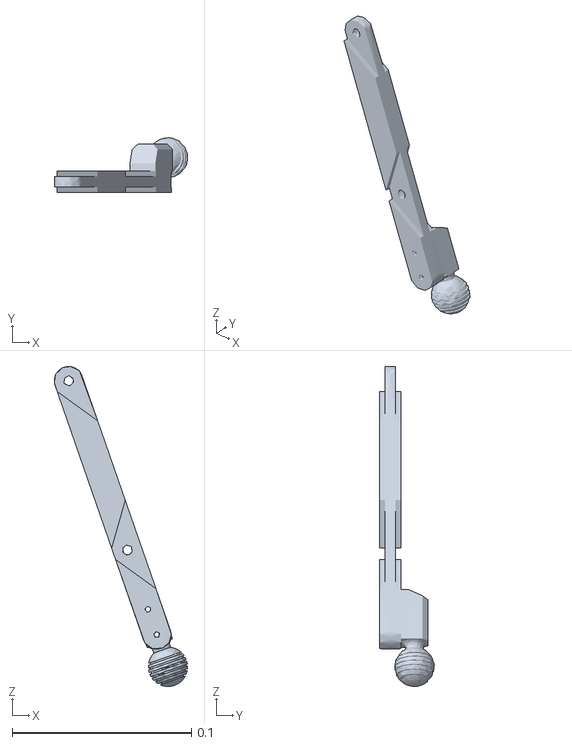
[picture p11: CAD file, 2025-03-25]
quadson_py/assets/whole_body/meshes/stl/rr_link2.stl
0.0744 x 0.0306 x 0.179

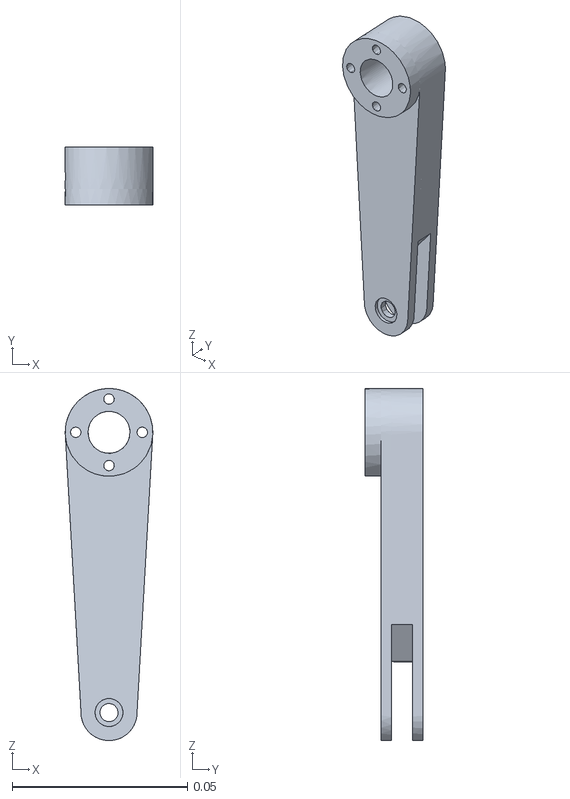
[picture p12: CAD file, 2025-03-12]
quadson_sim/assets/whole_body/meshes/stl/fl_link4_dummy.stl
0.025 x 0.0165 x 0.1

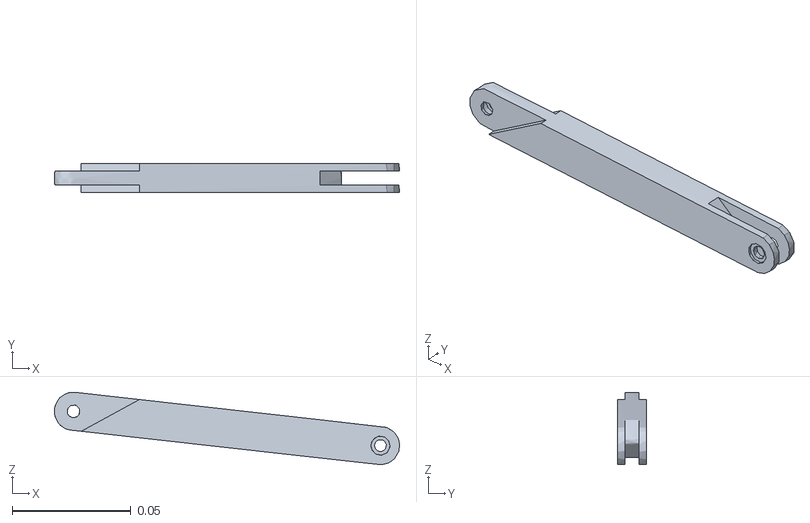
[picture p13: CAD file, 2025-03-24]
quadson_py/assets/single_leg/meshes/stl/link3.stl
0.145 x 0.012 x 0.0305

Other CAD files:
quadson_py/assets/single_leg/meshes/stl/link1.stl
quadson_py/assets/whole_body/meshes/stl/rl_link5.stl
quadson_py/assets/whole_body/meshes/stl/rr_link5.stl
quadson_py/assets/single_leg/meshes/stl/link4.stl
quadson_py/assets/whole_body/meshes/stl/rl_link2.stl
quadson_py/assets/single_leg/meshes/stl/link2.stl
quadson_py/assets/whole_body/meshes/stl/fl_link4.stl
quadson_py/assets/whole_body/meshes/stl/rr_link4.stl
quadson_py/assets/whole_body/meshes/stl/fr_link2.stl
quadson_py/assets/whole_body/meshes/stl/rl_link0.stl
quadson_py/assets/whole_body/meshes/stl/fr_link5.stl
quadson_py/assets/whole_body/meshes/stl/fr_link4.001.stl
quadson_py/assets/whole_body/meshes/stl/fr_link0.stl
quadson_py/assets/whole_body/meshes/stl/rl_link4.stl
quadson_py/assets/whole_body/meshes/stl/base_link.stl
quadson_py/assets/whole_body/meshes/stl/fl_link0.stl
quadson_py/assets/whole_body/meshes/stl/fl_link1.stl
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

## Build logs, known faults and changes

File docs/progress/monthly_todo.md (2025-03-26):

# Monthly ToDo

## 2025-03

- [ ] 學習 PPO
- [ ] 建立環境
- [ ] 實現基本行走
- 明確要解什麼問題（哪裡不穩定？想改善哪種策略？想讓狗更穩？更省電？）
- [ ] 整理目前技術成果：IK 模型、PyBullet 環境、初步控制結果
- [ ] 文獻閱讀（建資料庫）：主要關鍵詞如 `Sim-to-Real`, `Domain Randomization`, `PPO locomotion`, `SAC quadruped`, `reward shaping`, `transfer learning`

## 2025-04

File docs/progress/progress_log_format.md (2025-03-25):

# Progress Log

## Week (Date)

### Done

### Learnings

### Problems

### Next

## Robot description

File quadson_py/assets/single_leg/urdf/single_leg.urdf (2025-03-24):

<robot name="single_leg" version="1.0">
  <joint name="joint1" type="revolute">
    <limit lower="-3.14000" upper="3.14000" effort="0.00000" velocity="0.00000"/>
    <origin rpy="-1.57080 0.00000 0.00000" xyz="0.04100 0.01800 0.00003"/>
    <parent link="link0"/>
    <child link="link1"/>
    <axis xyz="0.00000 0.00000 1.00000"/>
  </joint>
  <joint name="joint2" type="revolute">
    <limit lower="-3.14000" upper="3.14000" effort="0.00000" velocity="0.00000"/>
    <origin rpy="-0.00000 0.00000 0.00000" xyz="0.07999 0.00001 0.00825"/>
    <parent link="link1"/>
    <child link="link2"/>
    <axis xyz="0.00000 0.00000 1.00000"/>
  </joint>
  <joint name="joint4" type="revolute">
    <limit lower="-3.14000" upper="3.14000" effort="0.00000" velocity="0.00000"/>
    <origin rpy="-0.00000 0.00000 0.00000" xyz="-0.00001 0.07999 0.00825"/>
    <parent link="link4"/>
    <child link="link3"/>
    <axis xyz="0.00000 0.00000 1.00000"/>
  </joint>
  <joint name="joint5" type="revolute">
    <limit lower="-3.14000" upper="3.14000" effort="0.00000" velocity="0.00000"/>
    <origin rpy="-1.57080 0.00000 0.00000" xyz="-0.04100 0.01800 -0.00000"/>
    <parent link="link0"/>
    <child link="link4"/>
    <axis xyz="0.00000 0.00000 1.00000"/>
  </joint>
  <link name="link0">
    <inertial>
      <inertia ixx="0.00010" ixy="0.00000" ixz="-0.00001" iyy="0.00059" iyz="-0.00000" izz="0.00053"/>
      <origin rpy="0.00000 0.00000 0.00000" xyz="-0.00003 -0.00190 -0.00002"/>
      <mass value="0.20000"/>
    </inertial>
    <visual name="link0_visual">
      <origin rpy="0.00000 0.00000 0.00000" xyz="0.00000 0.00000 0.00000"/>
      <geometry>
        <mesh filename="../meshes/stl/link0.stl" scale="1.00000 1.00000 1.00000"/>
      </geometry>
    </visual>
  </link>
  <link name="link1">
    <inertial>
      <inertia ixx="0.00001" ixy="-0.00002" ixz="-0.00000" iyy="0.00022" iyz="-0.00000" izz="0.00021"/>
      <origin rpy="0.00000 0.00000 0.00000" xyz="0.02888 0.00002 0.00661"/>
      <mass value="0.20000"/>
    </inertial>
    <visual name="link1_visual">
      <origin rpy="1.57080 0.00000 0.00000" xyz="0.00000 0.00000 0.00000"/>
      <material name="leg_linkage"/>
      <geometry>
        <mesh filename="../meshes/stl/link1.stl" scale="1.00000 1.00000 1.00000"/>
      </geometry>
    </visual>
  </link>
  <link name="link2">
    <inertial>
      <inertia ixx="0.00053" ixy="-0.00002" ixz="-0.00018" iyy="0.00058" iyz="-0.00005" izz="0.00008"/>
      <origin rpy="0.00000 0.00000 0.00000" xyz="-0.03247 0.09410 -0.00380"/>
      <mass value="0.20000"/>
    </inertial>
    <visual name="link2_visual">
      <origin rpy="1.57080 0.00000 0.00000" xyz="-0.03281 0.09447 0.00000"/>
      <geometry>
        <mesh filename="../meshes/stl/link2.stl" scale="1.00000 1.00000 1.00000"/>
      </geometry>
    </visual>
  </link>
  <link name="link3">
    <inertial>
      <inertia ixx="0.00001" ixy="-0.00000" ixz="0.00003" iyy="0.00032" iyz="0.00000" izz="0.00032"/>
      <origin rpy="0.00000 0.00000 0.00000" xyz="0.06459 0.00733 0.00000"/>
      <mass value="0.20000"/>
    </inertial>
    <visual name="link3_visual">
      <origin rpy="1.57080 0.00000 0.00000" xyz="0.12919 0.01447 -0.00000"/>
      <geometry>
        <mesh filename="../meshes/stl/link3.stl" scale="1.00000 1.00000 1.00000"/>
      </geometry>
    </visual>
  </link>
  <link name="link4">
    <inertial>
      <inertia ixx="0.00018" ixy="-0.00000" ixz="0.00000" iyy="0.00019" iyz="0.00001" izz="0.00001"/>
      <origin rpy="0.00000 0.00000 0.00000" xyz="-0.00001 0.02888 0.00661"/>
      <mass value="0.20000"/>
    </inertial>
    <visual name="link4_visual">
      <origin rpy="1.57080 0.00000 0.00000" xyz="-0.00001 0.07999 0.00825"/>
      <geometry>
        <mesh filename="../meshes/stl/link4.stl" scale="1.00000 1.00000 1.00000"/>
      </geometry>
    </visual>
  </link>
  <material name="leg_linkage">
    <color rgba="0.80000 0.80000 0.80000 1.00000"/>
  </material>
</robot>

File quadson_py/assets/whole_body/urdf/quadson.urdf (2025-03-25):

<robot name="quadson" version="1.0">
  <joint name="fl_joint0" type="revolute">
    <limit lower="-3.14000" upper="3.14000" effort="0.00000" velocity="0.00000"/>
    <origin rpy="-0.00000 1.57080 0.00000" xyz="0.20500 0.09541 0.00215"/>
    <parent link="base_link"/>
    <child link="fl_link0"/>
    <axis xyz="0.00000 0.00000 1.00000"/>
  </joint>
  <joint name="fl_joint1" type="revolute">
    <limit lower="-3.14000" upper="3.14000" effort="0.00000" velocity="0.00000"/>
    <origin rpy="-1.57080 -1.57080 0.00000" xyz="-0.00026 0.01767 -0.05190"/>
    <parent link="fl_link0"/>
    <child link="fl_link1"/>
    <axis xyz="0.00000 0.00000 1.00000"/>
  </joint>
  <joint name="fl_joint2" type="revolute">
    <limit lower="-3.14000" upper="3.14000" effort="0.00000" velocity="0.00000"/>
    <origin rpy="-0.00000 0.00000 0.00000" xyz="0.07999 0.00001 0.00825"/>
    <parent link="fl_link1"/>
    <child link="fl_link2"/>
    <axis xyz="0.00000 0.00000 1.00000"/>
  </joint>
  <joint name="fl_joint4" type="revolute">
    <limit lower="-3.14000" upper="3.14000" effort="0.00000" velocity="0.00000"/>
    <origin rpy="-0.00000 0.00000 0.00000" xyz="-0.00001 0.07999 0.00825"/>
    <parent link="fl_link5"/>
    <child link="fl_link4"/>
    <axis xyz="0.00000 0.00000 1.00000"/>
  </joint>
  <joint name="fl_joint5" type="revolute">
    <limit lower="-3.14000" upper="3.14000" effort="0.00000" velocity="0.00000"/>
    <origin rpy="-1.57080 -1.57080 0.00000" xyz="-0.00023 0.01767 -0.13390"/>
    <parent link="fl_link0"/>
    <child link="fl_link5"/>
    <axis xyz="0.00000 0.00000 1.00000"/>
  </joint>
  <joint name="fr_joint0" type="revolute">
    <limit lower="-3.14000" upper="3.14000" effort="0.00000" velocity="0.00000"/>
    <origin rpy="-0.00000 1.57080 0.00000" xyz="0.20500 -0.09380 0.00162"/>
    <parent link="base_link"/>
    <child link="fr_link0"/>
    <axis xyz="0.00000 0.00000 1.00000"/>
  </joint>
  <joint name="fr_joint1" type="revolute">
    <limit lower="-3.14000" upper="3.14000" effort="0.00000" velocity="0.00000"/>
    <origin rpy="-1.57080 -1.57080 0.00000" xyz="-0.00026 -0.01767 -0.05190"/>
    <parent link="fr_link0"/>
    <child link="fr_link1"/>
    <axis xyz="0.00000 0.00000 1.00000"/>
  </joint>
  <joint name="fr_joint2" type="revolute">
    <limit lower="-3.14000" upper="3.14000" effort="0.00000" velocity="0.00000"/>
    <origin rpy="-0.00000 0.00000 0.00000" xyz="0.07999 0.00001 -0.00825"/>
    <parent link="fr_link1"/>
    <child link="fr_link2"/>
    <axis xyz="0.00000 0.00000 1.00000"/>
  </joint>
  <joint name="fr_joint4" type="revolute">
    <limit lower="-3.14000" upper="3.14000" effort="0.00000" velocity="0.00000"/>
    <origin rpy="-0.00000 0.00000 0.00000" xyz="-0.00001 0.07999 -0.00825"/>
    <parent link="fr_link5"/>
    <child link="fr_link4"/>
    <axis xyz="0.00000 0.00000 1.00000"/>
  </joint>
  <joint name="fr_joint5" type="revolute">
    <limit lower="-3.14000" upper="3.14000" effort="0.00000" velocity="0.00000"/>
    <origin rpy="-1.57080 -1.57080 0.00000" xyz="-0.00023 -0.01767 -0.13390"/>
    <parent link="fr_link0"/>
    <child link="fr_link5"/>
    <axis xyz="0.00000 0.00000 1.00000"/>
  </joint>
  <joint name="rl_joint0" type="revolute">
    <limit lower="-3.14000" upper="3.14000" effort="0.00000" velocity="0.00000"/>
    <origin rpy="0.00000 -1.57080 0.00000" xyz="-0.20500 0.09541 0.00215"/>
    <parent link="base_link"/>
    <child link="rl_link0"/>
    <axis xyz="0.00000 0.00000 1.00000"/>
  </joint>
  <joint name="rl_joint1" type="revolute">
    <limit lower="-3.14000" upper="3.14000" effort="0.00000" velocity="0.00000"/>
    <origin rpy="1.57080 1.57080 0.00000" xyz="0.00026 0.01767 -0.05190"/>
    <parent link="rl_link0"/>
    <child link="rl_link1"/>
    <axis xyz="0.00000 0.00000 1.00000"/>
  </joint>
  <joint name="rl_joint2" type="revolute">
    <limit lower="-3.14000" upper="3.14000" effort="0.00000" velocity="0.00000"/>
    <origin rpy="0.00000 0.00000 -0.00000" xyz="-0.07999 -0.00001 -0.00825"/>
    <parent link="rl_link1"/>
    <child link="rl_link2"/>
    <axis xyz="0.00000 0.00000 1.00000"/>
  </joint>
  <joint name="rl_joint4" type="revolute">
    <limit lower="-3.14000" upper="3.14000" effort="0.00000" velocity="0.00000"/>
    <origin rpy="0.00000 0.00000 0.00000" xyz="0.00001 -0.07999 -0.00825"/>
    <parent link="rl_link5"/>
    <child link="rl_link4"/>
    <axis xyz="0.00000 0.00000 1.00000"/>
  </joint>
  <joint name="rl_joint5" type="revolute">
    <limit lower="-3.14000" upper="3.14000" effort="0.00000" velocity="0.00000"/>
    <origin rpy="1.57080 1.57080 0.00000" xyz="0.00023 0.01767 -0.13390"/>
    <parent link="rl_link0"/>
    <child link="rl_link5"/>
    <axis xyz="0.00000 0.00000 1.00000"/>
  </joint>
  <joint name="rr_joint0" type="revolute">
    <limit lower="-3.14000" upper="3.14000" effort="0.00000" velocity="0.00000"/>
    <origin rpy="0.00000 -1.57080 0.00000" xyz="-0.20500 -0.09459 0.00215"/>
    <parent link="base_link"/>
    <child link="rr_link0"/>
    <axis xyz="0.00000 0.00000 1.00000"/>
  </joint>
  <joint name="rr_joint1" type="revolute">
    <limit lower="-3.14000" upper="3.14000" effort="0.00000" velocity="0.00000"/>
    <origin rpy="1.57080 1.57080 0.00000" xyz="0.00011 -0.01748 -0.05170"/>
    <parent link="rr_link0"/>
    <child link="rr_link1"/>
    <axis xyz="0.00000 0.00000 1.00000"/>
  </joint>
  <joint name="rr_joint2" type="revolute">
    <limit lower="-3.14000" upper="3.14000" effort="0.00000" velocity="0.00000"/>
    <origin rpy="0.00000 0.00000 -0.00000" xyz="-0.07999 -0.00001 0.00825"/>
    <parent link="rr_link1"/>
    <child link="rr_link2"/>
    <axis xyz="0.00000 0.00000 1.00000"/>
  </joint>
  <joint name="rr_joint4" type="revolute">
    <limit lower="-3.14000" upper="3.14000" effort="0.00000" velocity="0.00000"/>
    <origin rpy="0.00000 0.00000 -0.00000" xyz="0.00001 -0.07999 0.00825"/>
    <parent link="rr_link5"/>
    <child link="rr_link4"/>
    <axis xyz="0.00000 0.00000 1.00000"/>
  </joint>
  <joint name="rr_joint5" type="revolute">
    <limit lower="-3.14000" upper="3.14000" effort="0.00000" velocity="0.00000"/>
    <origin rpy="1.57080 1.57080 0.00000" xyz="0.00008 -0.01748 -0.13370"/>
    <parent link="rr_link0"/>
    <child link="rr_link5"/>
    <axis xyz="0.00000 0.00000 1.00000"/>
  </joint>
  <link name="base_link">
    <inertial>
      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
      <origin rpy="0.00000 0.00000 0.00000" xyz="-0.00001 0.00040 -0.00279"/>
      <mass value="1.00000"/>
    </inertial>
    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
  </link>
  <link name="fl_link0">
    <inertial>
      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
      <origin rpy="0.00000 0.00000 0.00000" xyz="-0.00021 -0.00223 -0.09292"/>
      <mass value="0.50000"/>
    </inertial>
    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
  </link>
  <link name="fl_link1">
    <inertial>
      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
      <origin rpy="0.00000 0.00000 0.00000" xyz="0.02888 0.00002 0.00661"/>
      <mass value="0.30000"/>
    </inertial>
    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
  </link>
  <link name="fl_link2">
    <inertial>
      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
      <origin rpy="0.00000 0.00000 0.00000" xyz="-0.03247 0.09410 -0.00380"/>
      <mass value="0.30000"/>
    </inertial>
    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
  </link>
  <link name="fl_link4">
    <inertial>
      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
      <origin rpy="0.00000 0.00000 0.00000" xyz="0.06459 0.00733 0.00000"/>
      <mass value="0.30000"/>
    </inertial>
    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
  </link>
  <link name="fl_link5">
    <inertial>
      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
      <origin rpy="0.00000 0.00000 0.00000" xyz="-0.00001 0.02888 0.00661"/>
      <mass value="0.30000"/>
    </inertial>
    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
  </link>
  <link name="fr_link0">
    <inertial>
      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
      <origin rpy="0.00000 0.00000 0.00000" xyz="-0.00021 0.00223 -0.09292"/>
      <mass value="0.50000"/>
    </inertial>
    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
  </link>
  <link name="fr_link1">
    <inertial>
      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
      <origin rpy="0.00000 0.00000 0.00000" xyz="0.02888 0.00002 -0.00661"/>
      <mass value="0.30000"/>
    </inertial>
    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
  </link>
  <link name="fr_link2">
    <inertial>
      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
      <origin rpy="0.00000 0.00000 0.00000" xyz="-0.03247 0.09410 0.00380"/>
      <mass value="0.30000"/>
    </inertial>
    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

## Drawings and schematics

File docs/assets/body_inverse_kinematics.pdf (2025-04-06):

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

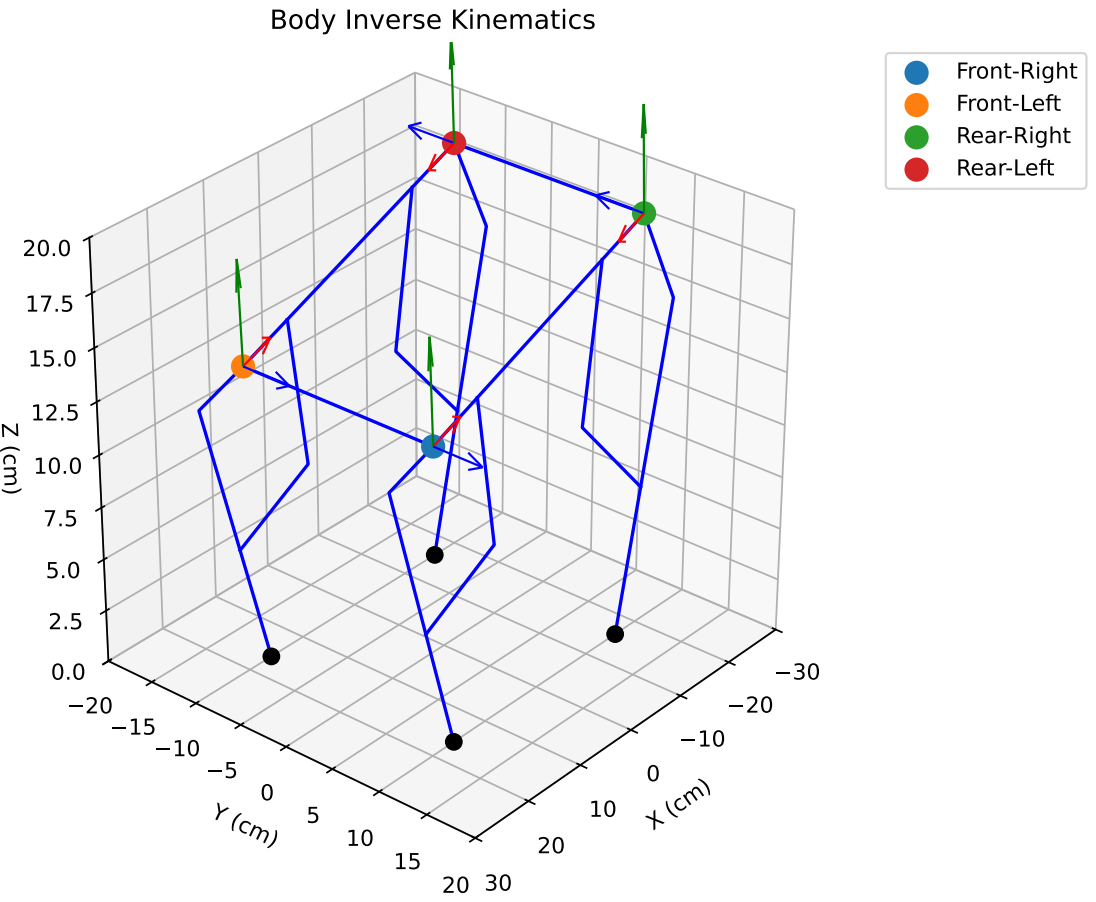
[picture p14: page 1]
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

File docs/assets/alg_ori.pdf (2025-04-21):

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

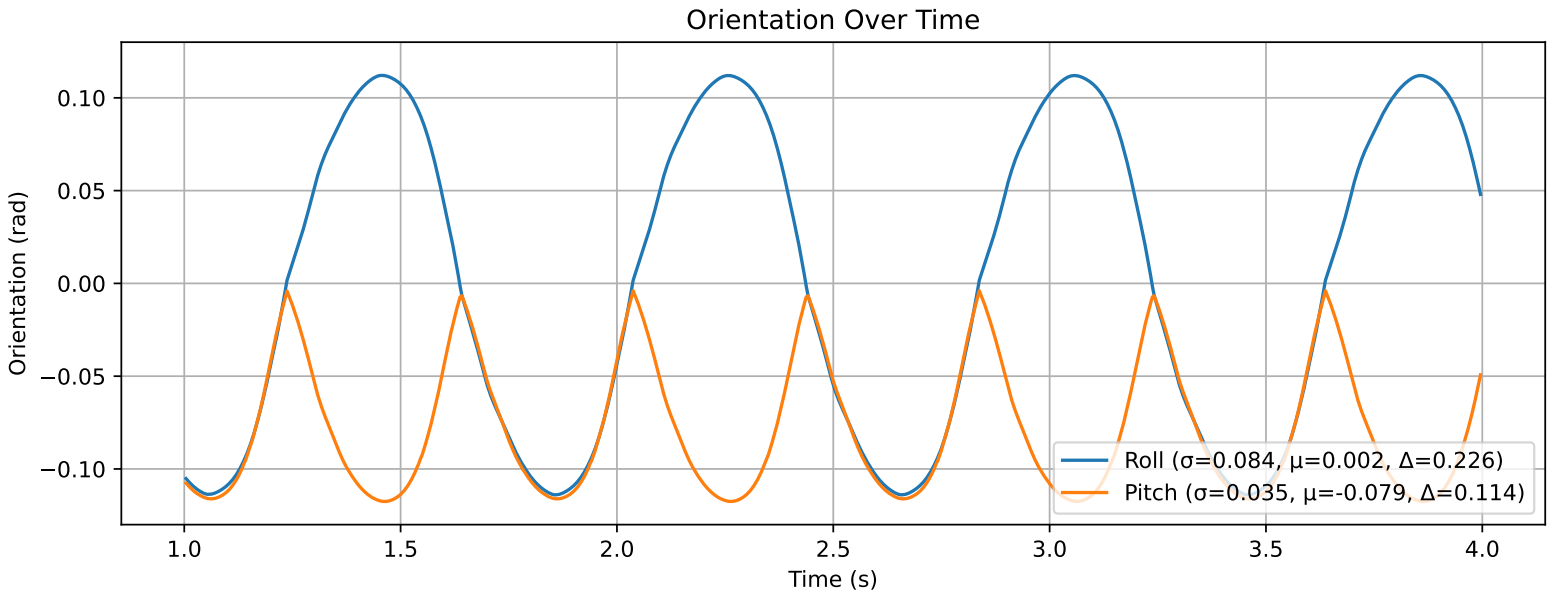
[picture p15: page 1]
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

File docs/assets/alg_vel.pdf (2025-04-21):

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

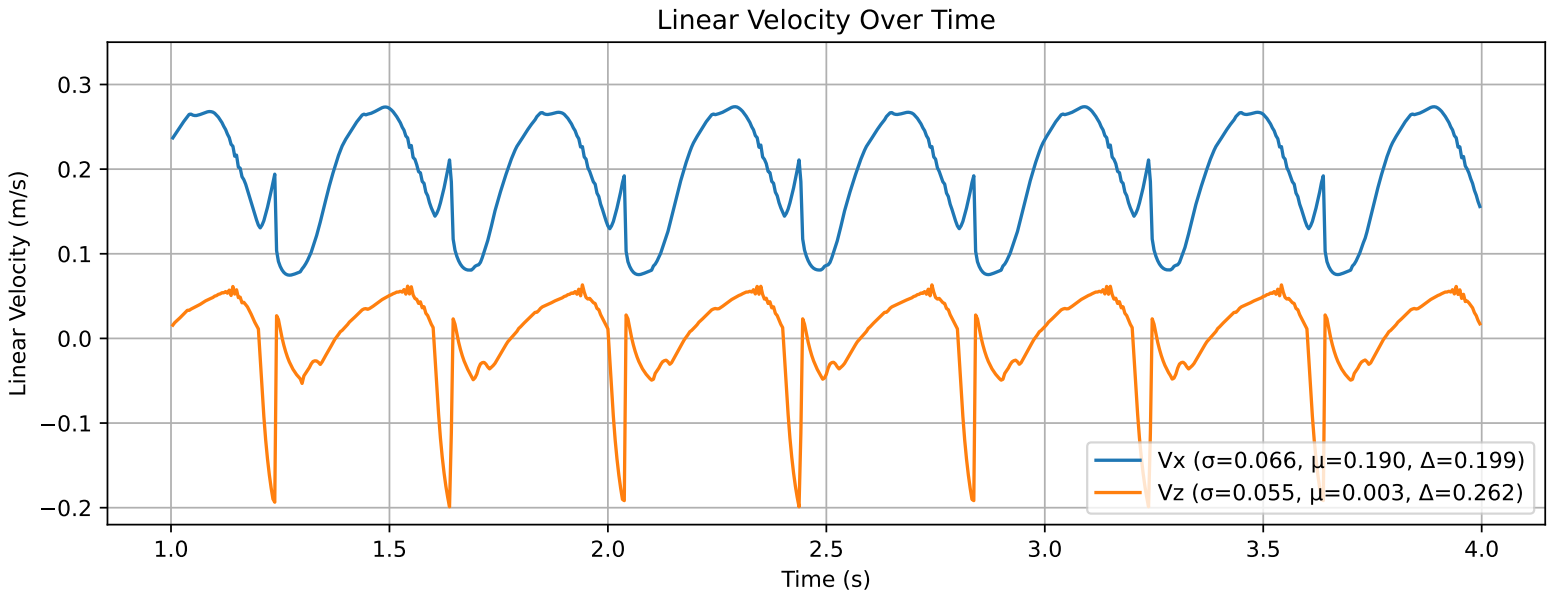
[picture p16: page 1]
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

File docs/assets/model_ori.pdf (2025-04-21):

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

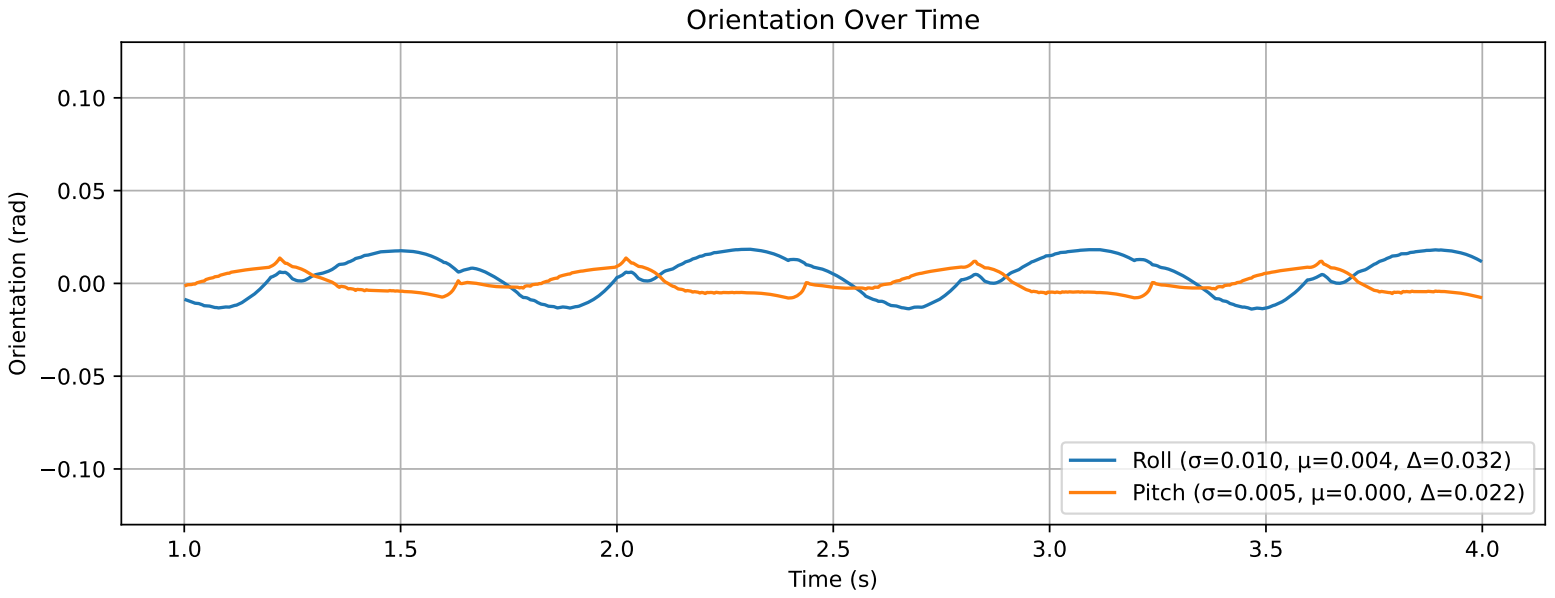
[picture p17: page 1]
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

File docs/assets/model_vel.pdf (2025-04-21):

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

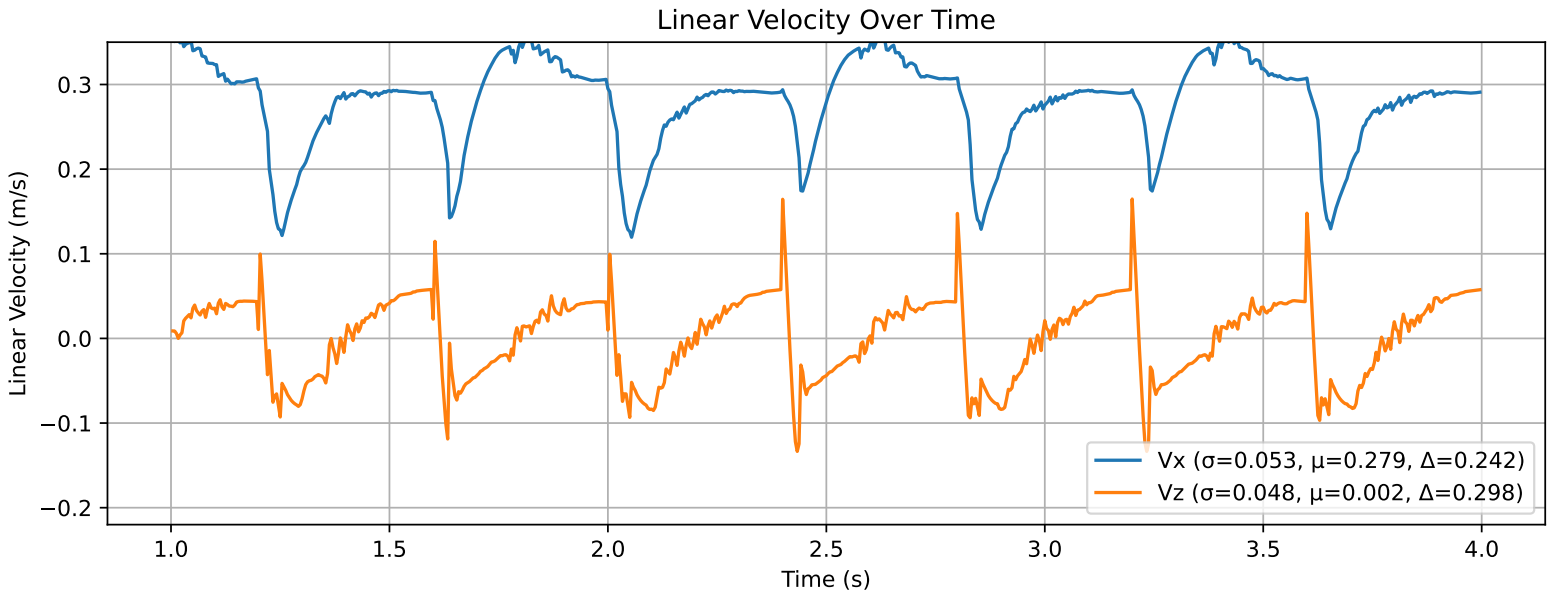
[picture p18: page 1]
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

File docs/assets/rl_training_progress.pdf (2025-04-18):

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

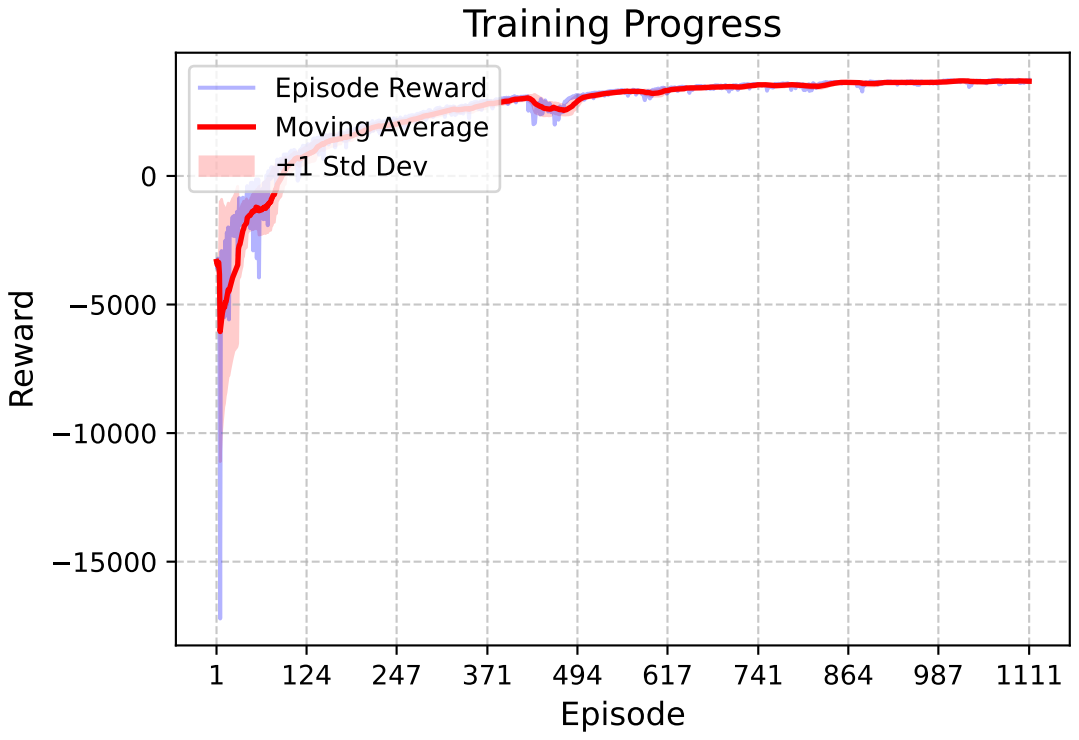
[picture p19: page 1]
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

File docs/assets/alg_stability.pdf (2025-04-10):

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

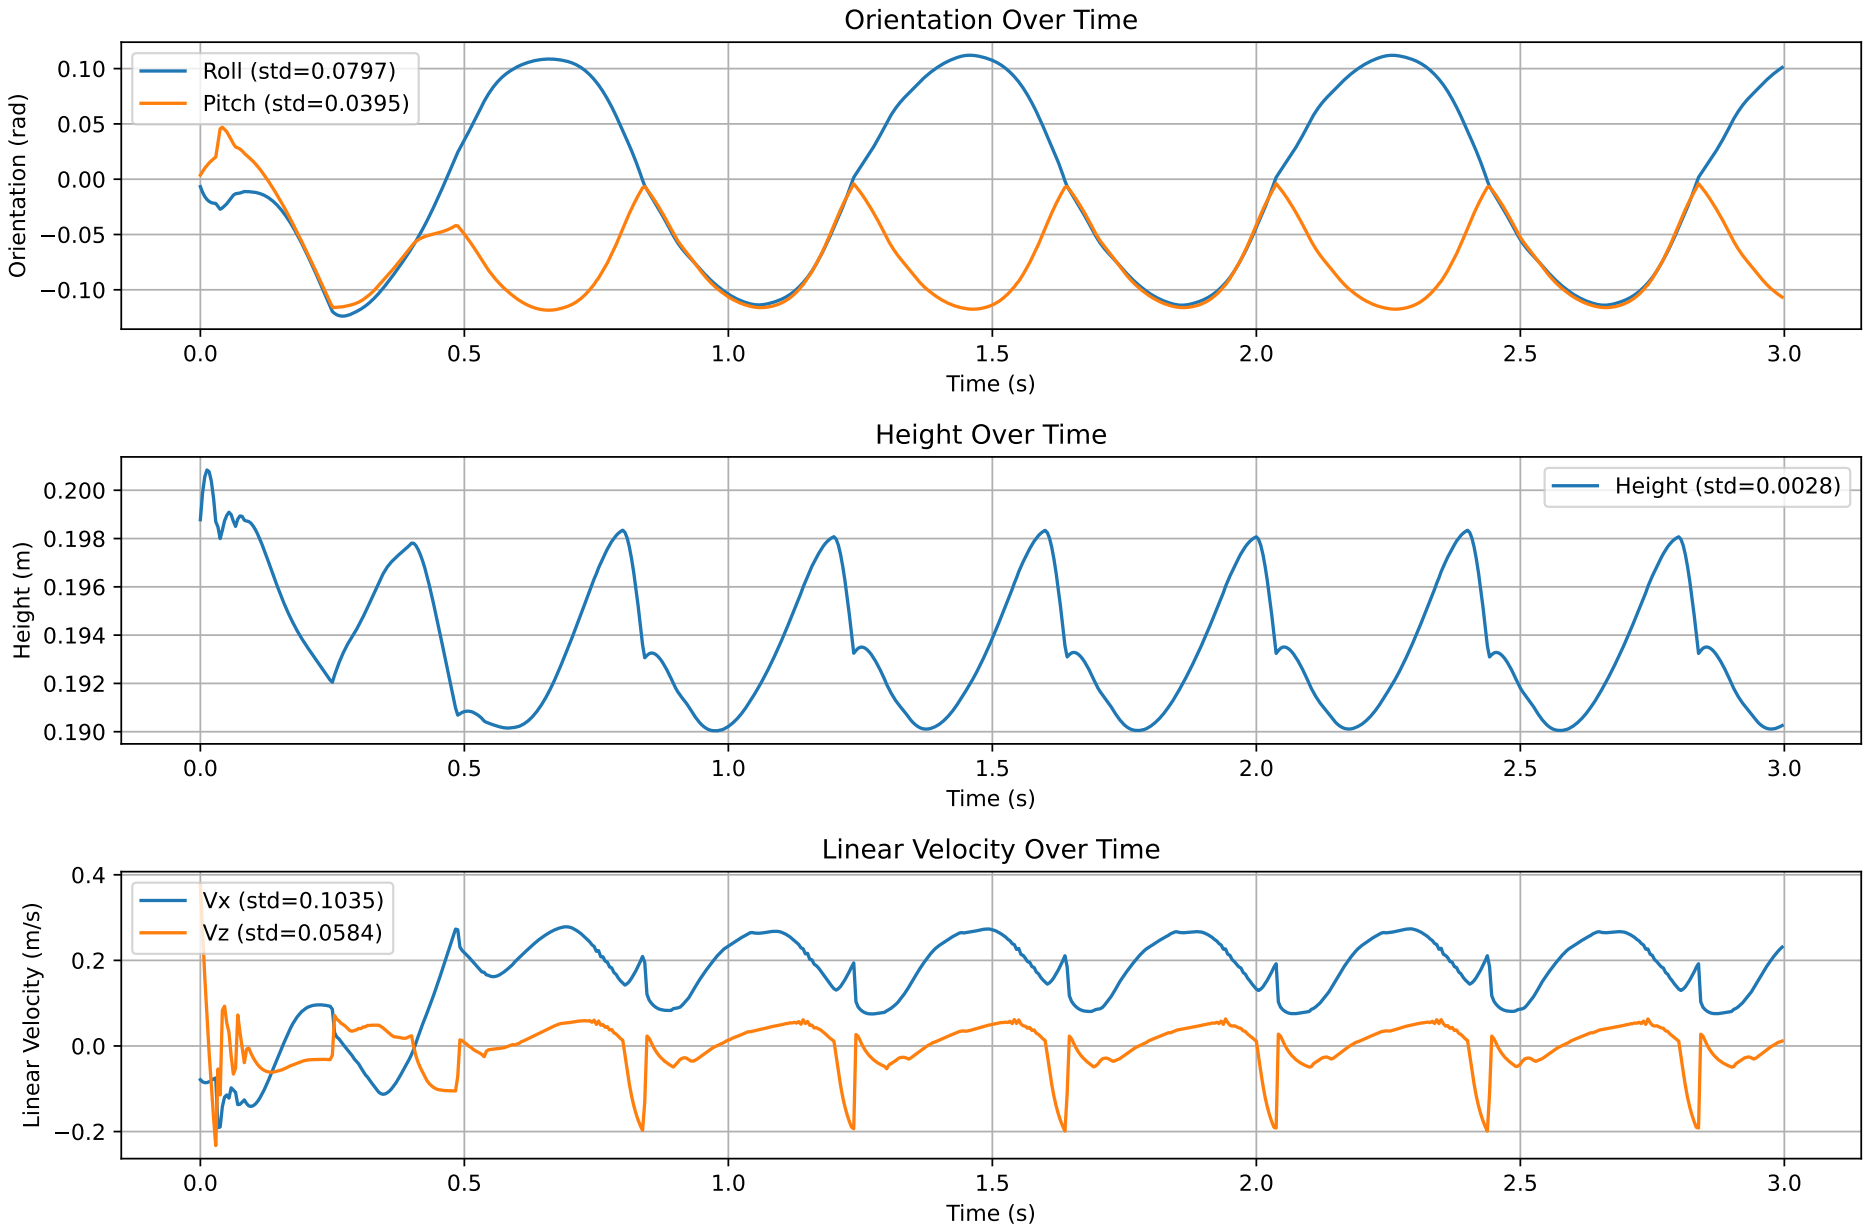
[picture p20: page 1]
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

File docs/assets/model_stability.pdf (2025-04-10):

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

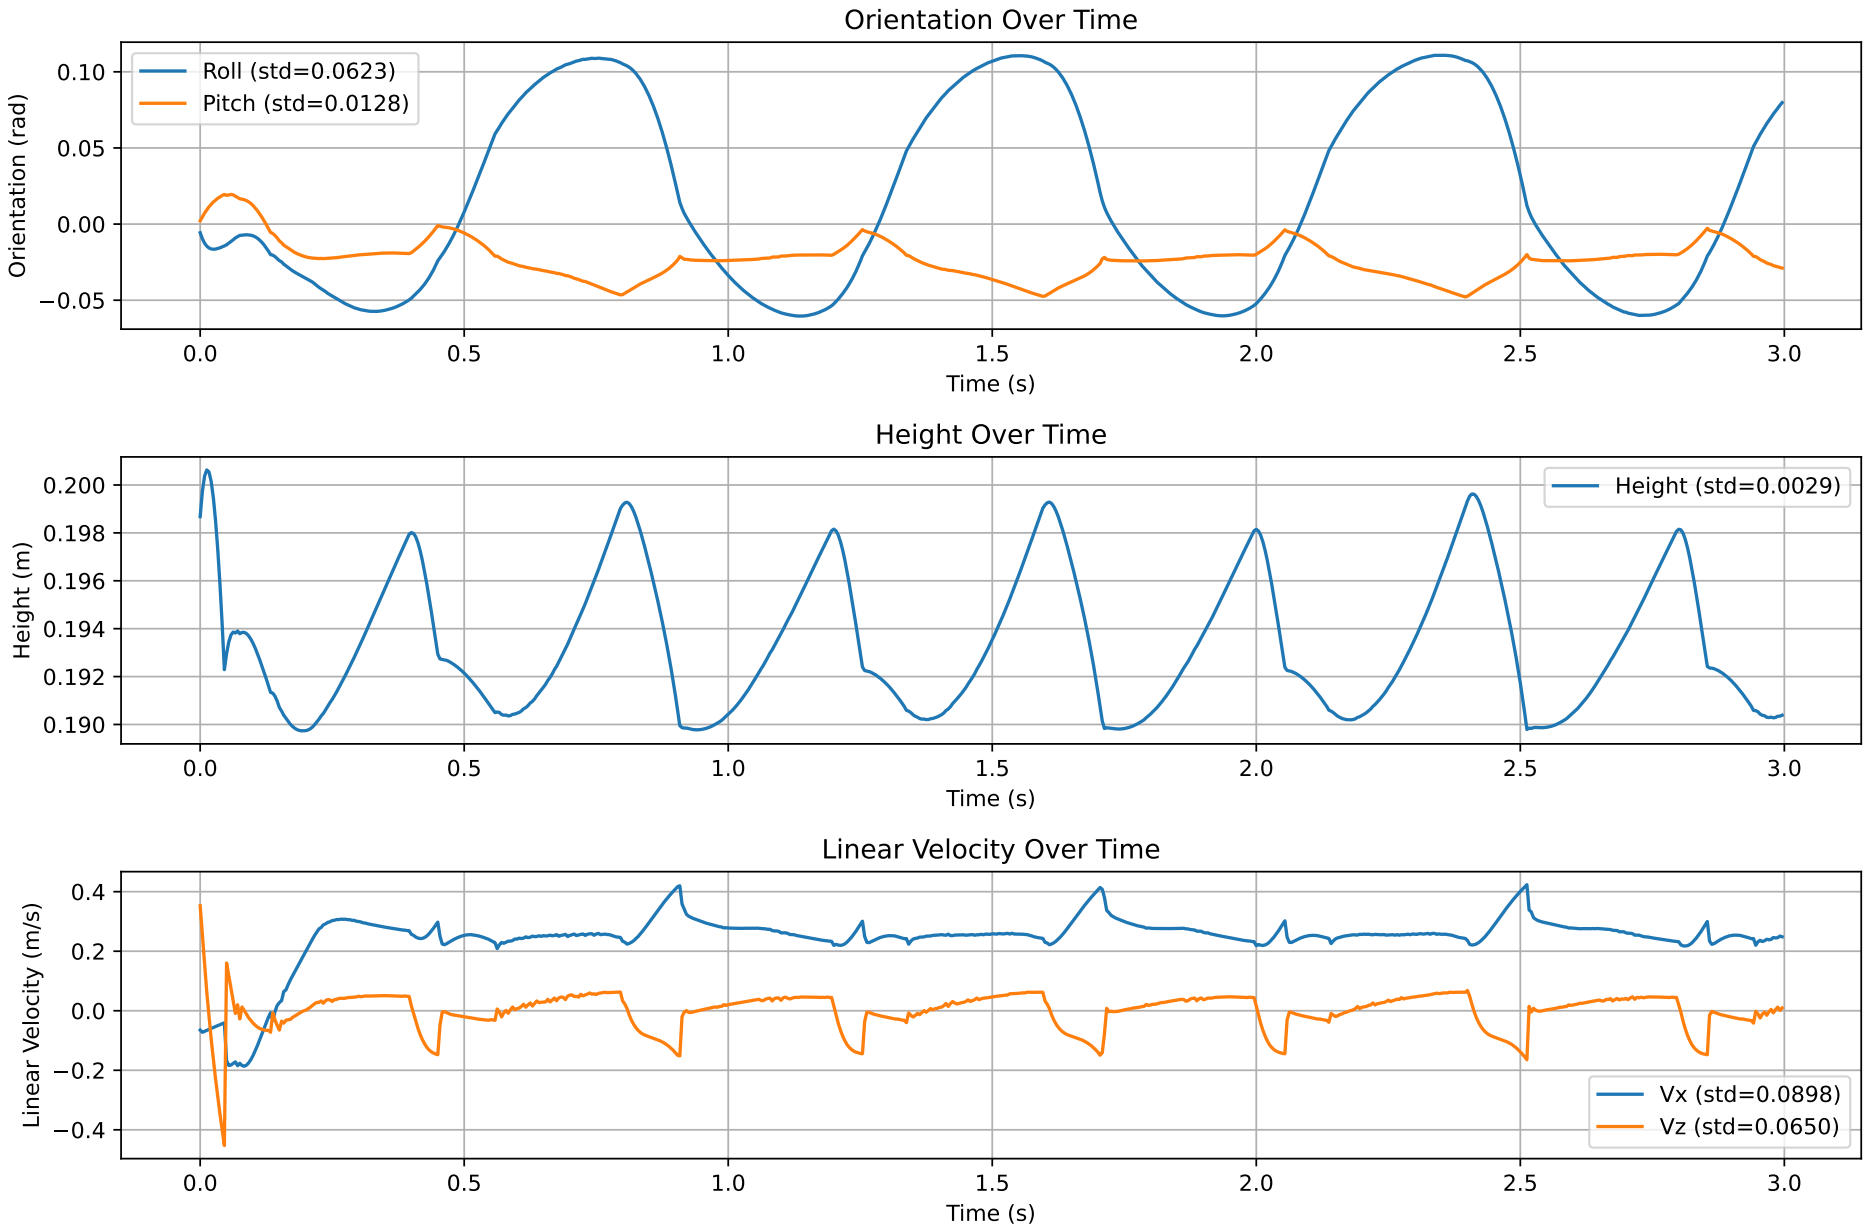
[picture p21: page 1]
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

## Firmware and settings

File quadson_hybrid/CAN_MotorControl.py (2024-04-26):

# import sys
# from cando import *


# dev_lists = list_scan()


# if len(dev_lists):
#     for dev in dev_lists:

#         serial_number = dev_get_serial_number_str(dev)

#         dev_info = dev_get_dev_info_str(dev)

#         print("Serial Number: " + serial_number + ', Dev Info: ' + dev_info)
# else:
#     print("Device not found!")
#     sys.exit(0)

from enum import IntEnum, auto
import struct
import math
import numpy as np

ID_STD_OFFSET = 6
ID_EXT_OFFSET = 24


class CAN_ID_TYPE(IntEnum):
	STANDARD = 0
	EXTENDED = 1

class CAN_STD_TYPE(IntEnum):
	CAN_STDID_ECHO = 0
	CAN_STDID_ALL_PARAM = auto()
	CAN_STDID_INFO_PARAM = auto()

	CAN_STDID_TORQUE_ENABLE = auto()
	CAN_STDID_STATE_MACHINE = auto()
	CAN_STDID_CONTROL_MODE = auto()

	CAN_STDID_GOAL_REVOLUTION = auto()
	CAN_STDID_GOAL_POSITION_DEG = auto()
	CAN_STDID_GOAL_VELOCITY_DPS = auto()
	CAN_STDID_GOAL_TORQUE_CURRENT_MA = auto()
	CAN_STDID_GOAL_FLUX_CURRENT_MA = auto()

	CAN_STDID_PRESENT_REVOLUTION = auto()
	CAN_STDID_PRESENT_POSITION_DEG = auto()
	CAN_STDID_PRESENT_VELOCITY_DPS = auto()
	CAN_STDID_PRESENT_TORQUE_CURRENT_MA = auto()
	CAN_STDID_PRESENT_FLUX_CURRENT_MA = auto()

	CAN_STDID_PRESENT_VOLTAGE = auto()
	CAN_STDID_PRESENT_TEMPERATURE = auto()
	CAN_STDID_MOVING = auto()

	CAN_STDID_GROUP0 = auto()
	CAN_STDID_GROUP1 = auto()
	CAN_STDID_GROUP2 = auto()
	CAN_STDID_GROUP3 = auto()

class CAN_EXT_TYPE(IntEnum):
	CAN_EXTID_MODEL_NUMBER = 0
	CAN_EXTID_VERSION = auto()
	CAN_EXTID_ID = auto()
	CAN_EXTID_BAUD_RATE = auto()
	CAN_EXTID_RECALIBRATE = auto()
	CAN_EXTID_GEARBOX_RATIO = auto()
	CAN_EXTID_MIN_POSITION_DEG = auto()
	CAN_EXTID_MAX_POSITION_DEG = auto()
	CAN_EXTID_MAX_VELOCITY_DPS = auto()
	CAN_EXTID_MAX_ACCELERATION_DPSS = auto()
	CAN_EXTID_MAX_CURRENT_MA = auto()
	CAN_EXTID_RESERVED_RAM_1 = auto()
	CAN_EXTID_TEMPERATURE_LIMIT = auto()
	CAN_EXTID_LOW_VOLTAGE_LIMIT = auto()
	CAN_EXTID_HIGH_VOLTAGE_LIMIT = auto()
	CAN_EXTID_MOVING_THRESHOLD_DPS = auto()
	CAN_EXTID_STATUS_RETURN_LVL = auto()
	CAN_EXTID_ALARM_LED = auto()
	CAN_EXTID_ALARM_SHUTDOWN = auto()
	CAN_EXTID_MOTOR_POLE_PAIRS = auto()
	CAN_EXTID_ELEC_SYNCHRO = auto()
	CAN_EXTID_MOTOR_OFFSET = auto()
	CAN_EXTID_POSITION_DEADZONE = auto()
	CAN_EXTID_INV_PHASE_MOTOR = auto()
	CAN_EXTID_INV_ROTATION = auto()
	CAN_EXTID_PID_POSITION_KP = auto()
	CAN_EXTID_PID_POSITION_KI = auto()
	CAN_EXTID_PID_POSITION_KD = auto()
	CAN_EXTID_PID_VELOCITY_KP = auto()
	CAN_EXTID_PID_VELOCITY_KI = auto()
	CAN_EXTID_PID_VELOCITY_KD = auto()
	CAN_EXTID_PID_VELOCITY_KFF = auto()
	CAN_EXTID_PID_ACCELERATION_KFF = auto()
	CAN_EXTID_PID_FLUX_CURRENT_KP = auto()
	CAN_EXTID_PID_FLUX_CURRENT_KI = auto()
	CAN_EXTID_PID_FLUX_CURRENT_KFF = auto()
	CAN_EXTID_PID_TORQUE_CURRENT_KP = auto()
	CAN_EXTID_PID_TORQUE_CURRENT_KI = auto()
	CAN_EXTID_PID_TORQUE_CURRENT_KFF = auto()
	CAN_EXTID_CAL_PHASE1_CURRENT_SENSE_MA = auto()
	CAN_EXTID_CAL_PHASE1_CURRENT_SENSE_OFFSET = auto()
	CAN_EXTID_CAL_PHASE2_CURRENT_SENSE_MA = auto()
	CAN_EXTID_CAL_PHASE2_CURRENT_SENSE_OFFSET = auto()
	CAN_EXTID_CAL_PHASE3_CURRENT_SENSE_MA = auto()
	CAN_EXTID_CAL_PHASE3_CURRENT_SENSE_OFFSET = auto()
	CAN_EXTID_CAL_VOLTAGE_SENSOR = auto()
	CAN_EXTID_TORQUE_ENABLE = auto()
	CAN_EXTID_STATE_MACHINE = auto()
	CAN_EXTID_CONTROL_MODE = auto()
	CAN_EXTID_GOAL_POSITION_DEG = auto()
	CAN_EXTID_GOAL_VELOCITY_DPS = auto()
	CAN_EXTID_GOAL_TORQUE_CURRENT_MA = auto()
	CAN_EXTID_GOAL_FLUX_CURRENT_MA = auto()
	CAN_EXTID_GOAL_REVOLUTION = auto()
	CAN_EXTID_GOAL_RESERVED_RAM_2 = auto()
	CAN_EXTID_GOAL_CLOSED_LOOP = auto()
	CAN_EXTID_PRESENT_REVOLUTION = auto()
	CAN_EXTID_PRESENT_POSITION_DEG = auto()
	CAN_EXTID_PRESENT_VELOCITY_DPS = auto()
	CAN_EXTID_PRESENT_TORQUE_CURRENT_MA = auto()
	CAN_EXTID_PRESENT_FLUX_CURRENT_MA = auto()
	CAN_EXTID_PRESENT_VOLTAGE = auto()
	CAN_EXTID_PRESENT_TEMPERATURE = auto()
	CAN_EXTID_MOVING = auto()
	CAN_EXTID_ALL_PARAM = auto()
	CAN_EXTID_INFO_PARAM = auto()

class CMD_TYPE(IntEnum):
	MODEL_NUMBER = 0
	VERSION = auto()
	ID = auto()
	BAUD_RATE = auto()
	RECALIBRATE = auto()
	GEARBOX_RATIO = auto()
	MIN_POSITION_DEG = auto()
	MAX_POSITION_DEG = auto()
	MAX_VELOCITY_DPS = auto()
	MAX_ACCELERATION_DPSS = auto()
	MAX_CURRENT_MA = auto()
	RESERVED_RAM_1 = auto()
	TEMPERATURE_LIMIT = auto()
	LOW_VOLTAGE_LIMIT = auto()
	HIGH_VOLTAGE_LIMIT = auto()
	MOVING_THRESHOLD_DPS = auto()
	STATUS_RETURN_LVL = auto()
	ALARM_LED = auto()
	ALARM_SHUTDOWN = auto()
	MOTOR_POLE_PAIRS = auto()
	ELEC_SYNCHRO = auto()
	MOTOR_OFFSET = auto()
	POSITION_DEADZONE = auto()
	INV_PHASE_MOTOR = auto()
	INV_ROTATION = auto()
	PID_POSITION_KP = auto()
	PID_POSITION_KI = auto()
	PID_POSITION_KD = auto()
	PID_VELOCITY_KP = auto()
	PID_VELOCITY_KI = auto()
	PID_VELOCITY_KD = auto()
	PID_VELOCITY_KFF = auto()
	PID_ACCELERATION_KFF = auto()
	PID_FLUX_CURRENT_KP = auto()
	PID_FLUX_CURRENT_KI = auto()
	PID_FLUX_CURRENT_KFF = auto()
	PID_TORQUE_CURRENT_KP = auto()
	PID_TORQUE_CURRENT_KI = auto()
	PID_TORQUE_CURRENT_KFF = auto()
	CAL_PHASE1_CURRENT_SENSE_MA = auto()
	CAL_PHASE1_CURRENT_SENSE_OFFSET = auto()
	CAL_PHASE2_CURRENT_SENSE_MA = auto()
	CAL_PHASE2_CURRENT_SENSE_OFFSET = auto()
	CAL_PHASE3_CURRENT_SENSE_MA = auto()
	CAL_PHASE3_CURRENT_SENSE_OFFSET = auto()
	CAL_VOLTAGE_SENSOR = auto()
	TORQUE_ENABLE = auto()
	CONTROL_MODE = auto()
	GOAL_REVOLUTION = auto()
	GOAL_POSITION_DEG = auto()
	GOAL_VELOCITY_DPS = auto()
	GOAL_TORQUE_CURRENT_MA = auto()
	GOAL_FLUX_CURRENT_MA = auto()
	GOAL_RESERVED_RAM_2 = auto()
	GOAL_CLOSED_LOOP = auto()
	PRESENT_REVOLUTION = auto()
	PRESENT_POSITION_DEG = auto()
	PRESENT_VELOCITY_DPS = auto()
	PRESENT_TORQUE_CURRENT_MA = auto()
	PRESENT_FLUX_CURRENT_MA = auto()
	PRESENT_VOLTAGE = auto()
	PRESENT_TEMPERATURE = auto()
	MOVING = auto()

Param_Dict = {
	CMD_TYPE.MODEL_NUMBER : 0,
	CMD_TYPE.VERSION : 0,
	CMD_TYPE.ID : 0,
	CMD_TYPE.BAUD_RATE : 0,
	CMD_TYPE.RECALIBRATE : 0,
	CMD_TYPE.GEARBOX_RATIO : 0,
	CMD_TYPE.MIN_POSITION_DEG : 0,
	CMD_TYPE.MAX_POSITION_DEG : 0,
	CMD_TYPE.MAX_VELOCITY_DPS : 0,
	CMD_TYPE.MAX_ACCELERATION_DPSS : 0,
	CMD_TYPE.MAX_CURRENT_MA : 0,
	CMD_TYPE.RESERVED_RAM_1 : 0,
	CMD_TYPE.TEMPERATURE_LIMIT : 0,
	CMD_TYPE.LOW_VOLTAGE_LIMIT : 0,
	CMD_TYPE.HIGH_VOLTAGE_LIMIT : 0,
	CMD_TYPE.MOVING_THRESHOLD_DPS : 0,
	CMD_TYPE.STATUS_RETURN_LVL : 0,
	CMD_TYPE.ALARM_LED : 0,
	CMD_TYPE.ALARM_SHUTDOWN : 0,
	CMD_TYPE.MOTOR_POLE_PAIRS : 0,
	CMD_TYPE.ELEC_SYNCHRO : 0,
	CMD_TYPE.MOTOR_OFFSET : 0,
	CMD_TYPE.POSITION_DEADZONE : 0,
	CMD_TYPE.INV_PHASE_MOTOR : 0,
	CMD_TYPE.INV_ROTATION : 0,
	CMD_TYPE.PID_POSITION_KP : 0,
	CMD_TYPE.PID_POSITION_KI : 0,
	CMD_TYPE.PID_POSITION_KD : 0,
	CMD_TYPE.PID_VELOCITY_KP : 0,
	CMD_TYPE.PID_VELOCITY_KI : 0,
	CMD_TYPE.PID_VELOCITY_KD : 0,
	CMD_TYPE.PID_VELOCITY_KFF : 0,
	CMD_TYPE.PID_ACCELERATION_KFF : 0,
	CMD_TYPE.PID_FLUX_CURRENT_KP : 0,
	CMD_TYPE.PID_FLUX_CURRENT_KI : 0,
	CMD_TYPE.PID_FLUX_CURRENT_KFF : 0,
	CMD_TYPE.PID_TORQUE_CURRENT_KP : 0,
	CMD_TYPE.PID_TORQUE_CURRENT_KI : 0,
	CMD_TYPE.PID_TORQUE_CURRENT_KFF : 0,
	CMD_TYPE.CAL_PHASE1_CURRENT_SENSE_MA : 0,
	CMD_TYPE.CAL_PHASE1_CURRENT_SENSE_OFFSET : 0,
	CMD_TYPE.CAL_PHASE2_CURRENT_SENSE_MA : 0,
	CMD_TYPE.CAL_PHASE2_CURRENT_SENSE_OFFSET : 0,
	CMD_TYPE.CAL_PHASE3_CURRENT_SENSE_MA : 0,
	CMD_TYPE.CAL_PHASE3_CURRENT_SENSE_OFFSET : 0,
	CMD_TYPE.CAL_VOLTAGE_SENSOR : 0,
	CMD_TYPE.TORQUE_ENABLE : 0,
	CMD_TYPE.CONTROL_MODE : 0,
	CMD_TYPE.GOAL_REVOLUTION : 0,
	CMD_TYPE.GOAL_POSITION_DEG : 0,
	CMD_TYPE.GOAL_VELOCITY_DPS : 0,
	CMD_TYPE.GOAL_TORQUE_CURRENT_MA : 0,
	CMD_TYPE.GOAL_FLUX_CURRENT_MA : 0,
	CMD_TYPE.GOAL_RESERVED_RAM_2 : 0,
	CMD_TYPE.GOAL_CLOSED_LOOP : 0,
	CMD_TYPE.PRESENT_REVOLUTION : 0,
	CMD_TYPE.PRESENT_POSITION_DEG : 0,
	CMD_TYPE.PRESENT_VELOCITY_DPS : 0,
	CMD_TYPE.PRESENT_TORQUE_CURRENT_MA : 0,
	CMD_TYPE.PRESENT_FLUX_CURRENT_MA : 0,
	CMD_TYPE.PRESENT_VOLTAGE : 0,
	CMD_TYPE.PRESENT_TEMPERATURE : 0,
	CMD_TYPE.MOVING : 0,
}

def msg_error(rec_frame):
	if rec_frame.can_id & CANDO_ID_ERR:
		error_code, err_tx, err_rx = parse_err_frame(rec_frame)
		print("Error: ")
		print(error_code)
		if error_code & CAN_ERR_BUSOFF:
			print(" CAN_ERR_BUSOFF")
		if error_code & CAN_ERR_RX_TX_WARNING:
			print(" CAN_ERR_RX_TX_WARNING")
		if error_code & CAN_ERR_RX_TX_PASSIVE:
			print(" CAN_ERR_RX_TX_PASSIVE")
		if error_code & CAN_ERR_OVERLOAD:
			print(" CAN_ERR_OVERLOAD")
		if error_code & CAN_ERR_STUFF:
			print(" CAN_ERR_STUFF")
		if error_code & CAN_ERR_FORM:
			print(" CAN_ERR_FORM")
		if error_code & CAN_ERR_ACK:
			print(" CAN_ERR_ACK")
		if error_code & CAN_ERR_BIT_RECESSIVE:
			print(" CAN_ERR_BIT_RECESSIVE")
		if error_code & CAN_ERR_BIT_DOMINANT:
			print(" CAN_ERR_BIT_DOMINANT")
		if error_code & CAN_ERR_CRC:
			print(" CAN_ERR_CRC")
			print(" err_tx: " + str(err_tx))
			print(" err_rx: " + str(err_rx))

		return True

	else:
		return False



class Can_msg_package(object):
	def __init__(self, motor_id, id_type, msg_id, data):
		self.motor_id = motor_id
		self.id_type = id_type
		self.msg_id = msg_id 
		self.data = data

class Can_motor(object):
	def __init__(self, motor_id, exist):
		self.motor_id = motor_id
		self.exist = exist
		self.params = dict(Param_Dict)

	def can_motor_param_update(self, id_type, msg_id, value):
		if id_type == CAN_ID_TYPE.EXTENDED:
			self.params[msg_id] = value
		else:
			if msg_id == CAN_STD_TYPE.CAN_STDID_TORQUE_ENABLE:
				self.params[CMD_TYPE.TORQUE_ENABLE.value] = value
			elif msg_id == CAN_STD_TYPE.CAN_STDID_STATE_MACHINE:
				self.params[CMD_TYPE.STATE_MACHINE.value] = value
			elif msg_id == CAN_STD_TYPE.CAN_STDID_CONTROL_MODE:
				self.params[CMD_TYPE.CONTROL_MODE.value] = value

			elif msg_id == CAN_STD_TYPE.CAN_STDID_GOAL_REVOLUTION:
				self.params[CMD_TYPE.GOAL_REVOLUTION.value] = value
			elif msg_id == CAN_STD_TYPE.CAN_STDID_GOAL_POSITION_DEG:
				self.params[CMD_TYPE.GOAL_POSITION_DEG.value] = value
			elif msg_id == CAN_STD_TYPE.CAN_STDID_GOAL_VELOCITY_DPS:
				self.params[CMD_TYPE.GOAL_VELOCITY_DPS.value] = value
			elif msg_id == CAN_STD_TYPE.CAN_STDID_GOAL_TORQUE_CURRENT_MA:
				self.params[CMD_TYPE.GOAL_TORQUE_CURRENT_MA.value] = value
			elif msg_id == CAN_STD_TYPE.CAN_STDID_GOAL_FLUX_CURRENT_MA:
				self.params[CMD_TYPE.GOAL_FLUX_CURRENT_MA.value] = value

			elif msg_id == CAN_STD_TYPE.CAN_STDID_PRESENT_REVOLUTION:
				self.params[CMD_TYPE.PRESENT_REVOLUTION.value] = value
			elif msg_id == CAN_STD_TYPE.CAN_STDID_PRESENT_POSITION_DEG:
				self.params[CMD_TYPE.PRESENT_POSITION_DEG.value] = value
			elif msg_id == CAN_STD_TYPE.CAN_STDID_PRESENT_VELOCITY_DPS:
				self.params[CMD_TYPE.PRESENT_VELOCITY_DPS.value] = value
			elif msg_id == CAN_STD_TYPE.CAN_STDID_PRESENT_TORQUE_CURRENT_MA:
				self.params[CMD_TYPE.PRESENT_TORQUE_CURRENT_MA.value] = value
			elif msg_id == CAN_STD_TYPE.CAN_STDID_PRESENT_FLUX_CURRENT_MA:
				self.params[CMD_TYPE.PRESENT_FLUX_CURRENT_MA.value] = value

			elif msg_id == CAN_STD_TYPE.CAN_STDID_PRESENT_VOLTAGE:
				self.params[CMD_TYPE.PRESENT_VOLTAGE.value] = value
			elif msg_id == CAN_STD_TYPE.CAN_STDID_PRESENT_TEMPERATURE:
				self.params[CMD_TYPE.PRESENT_TEMPERATURE.value] = value
			elif msg_id == CAN_STD_TYPE.CAN_STDID_MOVING:
				self.params[CMD_TYPE.MOVING.value] = value

	def can_motor_get_param(self, param_id):

		return self.params[param_id.value]



import threading	
import os	
class Can_motor_manager(object):
	def __init__(self):
		self.dev_lists = None
		self.motor_list = [None]*12
		for x in range(12):
			self.motor_list[x] = Can_motor(x, False)
		self.rec_frame = Frame()

		self.connect_can_device()
		self.thread_pause_event = threading.Event()
		self.thread_stop_event = threading.Event()
		self.reading_thread = threading.Thread(target = self.can_read_handle)

		self.thread_stop_event.set()
		self.reading_thread.start()

	def connect_can_device(self):
		self.dev_lists = list_scan()

		if len(self.dev_lists) == 0:
			print("Device not found!")
			sys.exit(0)

		if os.name == 'posix':  # for linux os
			if self.dev_lists[0].is_kernel_driver_active(0):
				reattach = True
				self.dev_lists[0].detach_kernel_driver(0)

		# set baudrate: 500K, sample point: 87.5%
		dev_set_timing(self.dev_lists[0], 1, 12, 6, 1, 6)

		dev_start(self.dev_lists[0], CANDO_MODE_NORMAL|CANDO_MODE_NO_ECHO_BACK)

	def disconnect_can_device(self):
		self.thread_stop_event.clear()
		dev_stop(self.dev_lists[0])

	def set_auto_receive(self, enable):
		if enable:
			self.thread_pause_event.set()
		else:
			self.thread_pause_event.clear()

	def scan_motors(self):
		print("Scaning...")

		for i in range(1,13):
			send_frame = Frame()
			send_frame.can_id = 0x00 | (i<<6)
			send_frame.can_id |= CANDO_ID_RTR
			# send_frame.can_dlc = 8
			# send_frame.data = [0x01, 0x02, 0x03, 0x04, 0x05, 0x06, 0x07, 0x08]
			dev_frame_send(self.dev_lists[0], send_frame)
			# print("scannnig "+str(i))
			time.sleep(0.001)

			if dev_frame_read(self.dev_lists[0], self.rec_frame, 1):
				if (not msg_error(self.rec_frame)):
					can_pack = self.decode_msg(self.rec_frame)
					if i == can_pack.motor_id:
						self.motor_list[i-1].exist = True
						print("Receive from motor " + str(i))
					else:
						print("Scanning error")
						self.disconnect_can_device()
						sys.exit(0)

			else:
				self.motor_list[i-1].exist = False
				print("Motor " + str(i) + " no response")

		for x in range(10):
			dev_frame_read(self.dev_lists[0], self.rec_frame, 1)


	def decode_msg(self, rec_frame):
		# print(" is_extend : " + ("True" if self.rec_frame.can_id & CANDO_ID_EXTENDED else "False"))
		# print(" is_rtr : " + ("True" if self.rec_frame.can_id & CANDO_ID_RTR	else "False"))
		# print(" can_id : " + str(self.rec_frame.can_id & CANDO_ID_MASK))
		can_id = self.rec_frame.can_id & CANDO_ID_MASK
		can_dlc = self.rec_frame.can_dlc
		group_mag = False
		if (self.rec_frame.can_id & CANDO_ID_EXTENDED):
			motor_id = can_id>>24
			id_type = CAN_ID_TYPE.EXTENDED
			msg_id = can_id & 0xFFFFF
			value = struct.unpack("<h",bytes(self.rec_frame.data[0:2]))[0]
			# print("from motor " + str(motor_id) + " get msg: " + str(CAN_EXT_TYPE(msg_id)) + " value: " + str(value))

		else:
			motor_id = can_id>>6
			if (motor_id>>10 > 0):
				group_mag = true
			id_type = CAN_ID_TYPE.STANDARD
			msg_id = can_id & 0x1F
			value = struct.unpack("<h",bytes(self.rec_frame.data[0:2]))[0]
			# print("from motor " + str(motor_id) + " get msg: " + str(CAN_STD_TYPE(msg_id)) + " value: " + str(value))

		if (group_mag):
			# TODO: add group msg handle
			pass

		self.motor_list[motor_id-1].can_motor_param_update(id_type, msg_id, value)
		
		return Can_msg_package(motor_id, id_type, msg_id, value)

	def can_read_handle(self):
		while self.thread_stop_event.isSet():
			self.thread_pause_event.wait()
			if dev_frame_read(self.dev_lists[0], self.rec_frame, 1):
				if (not msg_error(self.rec_frame)):
					self.decode_msg(self.rec_frame)
				else:
					print("reading error")
					self.disconnect_can_device()


	def send_motor_cmd(self, motor_index, cmd, value):

		if self.motor_list[motor_index-1].exist == False:
			print("Motor unconnected")
			return

		send_frame = Frame()
		
		if (cmd.__class__) == CAN_STD_TYPE:
			send_frame.can_id = 0x00 | (motor_index << ID_STD_OFFSET) | cmd.value
		else:
			send_frame.can_id = 0x00 | (motor_index << ID_EXT_OFFSET) | cmd.value
			send_frame.can_id |= CANDO_ID_EXTENDED

		send_frame.can_dlc = 2
		send_frame.data = [value>>8, value&0xFF, 0x00, 0x00, 0x00, 0x00, 0x00, 0x00]
		dev_frame_send(self.dev_lists[0], send_frame)
		# print("sending message id:" + str(send_frame.can_id))

	def can_motor_manager_get_angle(self, motor_id):
		self.send_motor_cmd(motor_id, CAN_STD_TYPE.CAN_STDID_PRESENT_REVOLUTION, 0)
		self.send_motor_cmd(motor_id, CAN_STD_TYPE.CAN_STDID_PRESENT_POSITION_DEG, 0)
		revolution = self.motor_list[motor_id-1].can_motor_get_param(CMD_TYPE.PRESENT_REVOLUTION)
		angle_16 = self.motor_list[motor_id-1].can_motor_get_param(CMD_TYPE.PRESENT_POSITION_DEG)
		# print("rev: " + str(revolution) + "  angle: " + str(angle_16))

		angle = (revolution + ( (angle_16) / 65536))/71.96 * 2*math.pi
		# print("degree: " + str(math.degrees(angle)))
		return angle

	def can_motor_manager_get_omega(self, motor_id):
		self.send_motor_cmd(motor_id, CAN_STD_TYPE.CAN_STDID_PRESENT_VELOCITY_DPS, 0)
		velocity_01 = self.motor_list[motor_id-1].can_motor_get_param(CMD_TYPE.PRESENT_VELOCITY_DPS)

		omega = (((velocity_01*10) / 65536))/71.96 * 2*math.pi
		# print("omega: " + str(omega))
		return omega

import numpy
class Leg(object):
	"""docstring for Leg"""
	def __init__(self, 
				# motor_1_obj, 
				# motor_2_obj,
				motors_distance=0.082,
				arm_a=0.08, 
				arm_b=0.13, 
				arm_c=0.08, 
				arm_d=0.10, 
				arm_e=0.066):

		# self.motor_1 = motor_1_obj
		# self.motor_2 = motor_2_obj
		self.motors_distance = motors_distance
		self.arm_a = arm_a
		self.arm_b = arm_b
		self.arm_c = arm_c
		self.arm_d = arm_d
		self.arm_e = arm_e

		self.pos = [0, 0, 0]
		self.vel = [0, 0, 0]
		self.angle = [0, 0, 0]
		self.omega = [0, 0, 0]


	def calc_r(self, a, b):
		return math.sqrt(a**2+b**2)

	def leg_pos2rad(self, pos):

		x = pos[0]
		y = pos[1]
		z = pos[2]

		angle_m1 = math.atan2(y, -z)
		zp = -self.calc_r(y, z)
		r_m3 = self.calc_r((self.motors_distance-x), zp)
		theta_m3 = math.atan2((self.motors_distance-x), -zp)
		psi_m3 = math.acos(( (self.arm_d+self.arm_e)**2 - self.arm_c**2 - r_m3**2 )/( -2*self.arm_c*r_m3 ))
		angle_m3 = psi_m3 - theta_m3
		beta_m3 = math.acos(( r_m3**2 - (self.arm_d+self.arm_e)**2 - self.arm_c**2 )/( -2*self.arm_c*(self.arm_d+self.arm_e) ))
		r_m3p = math.sqrt(self.arm_c**2 + self.arm_d**2 - 2*self.arm_c*self.arm_d*math.cos(beta_m3))
		psi_m3p = math.acos(( self.arm_d**2 - self.arm_c**2 - r_m3p**2 )/( -2*self.arm_c*r_m3p ))
		theta_m3p = psi_m3p - angle_m3
		r_m2 = self.calc_r((self.motors_distance - r_m3p*math.sin(theta_m3p)), -r_m3p*math.cos(theta_m3p))
		psi_m2 = math.acos(( self.arm_b**2 - self.arm_a**2 - r_m2**2 )/( -2*self.arm_a*r_m2 ))
		theta_m2 = math.atan2((self.motors_distance - r_m3p*math.sin(theta_m3p)), r_m3p*math.cos(theta_m3p))
		angle_m2 = psi_m2 - theta_m2
		# print(math.degrees(angle_m1))
		# print(math.degrees(angle_m2))
		# print(math.degrees(angle_m3))

		return np.array([angle_m1, angle_m2, angle_m3])


	def leg_pos_grad(self, pos):
		shift = 1e-8

		x = pos[0]
		y = pos[1]
		z = pos[2]
		
		x_plus = self.leg_pos2rad([x + shift, y, z])
		x_minus = self.leg_pos2rad([x - shift, y, z])
		x_grad = (0.5 * (x_plus - x_minus))/shift

		y_plus = self.leg_pos2rad([x, y + shift, z])
		y_minus = self.leg_pos2rad([x, y - shift, z])
		y_grad = (0.5 * (y_plus - y_minus))/shift

		z_plus = self.leg_pos2rad([x, y, z + shift])
		z_minus = self.leg_pos2rad([x, y, z - shift])
		z_grad = (0.5 * (z_plus - z_minus))/shift

		# print(x_grad)
		# print(y_grad)
		# print(z_grad)

		jacobian = np.matrix([x_grad, y_grad, z_grad])
		# print(jacobian)

		return jacobian

	def leg_vel2omega(self, pos, vel):
		jacobian = self.leg_pos_grad(pos)
		omega = vel*jacobian
		return omega


	def leg_rad2pos(self, angle):
		
		angle_m1 = angle[0]
		angle_m2 = angle[1]
		angle_m3 = angle[2]
		
		# f = math.sqrt(self.arm_a**2 + self.motors_distance**2 - 2*self.arm_a*self.motors_distance*math.cos(angle_m2+math.pi/2))
		f = math.sqrt(self.arm_a**2 + self.motors_distance**2 - 2*self.arm_a*self.motors_distance*math.cos(angle_m2+math.pi/2))
		g = self.calc_r(-self.arm_a*math.sin(angle_m2)-(self.motors_distance+self.arm_c*math.sin(angle_m3)), 
						-self.arm_a*math.cos(angle_m2)-(-self.arm_c*math.cos(angle_m3))) 
		psi = math.acos((f**2-self.arm_c**2-g**2)/(-2*self.arm_c*g))
		psi_1 = math.acos((self.arm_b**2-self.arm_d**2-g**2)/(-2*self.arm_d*g))
		psi = psi + psi_1

		x = self.motors_distance + self.arm_c*math.sin(angle_m3) - (self.arm_d+self.arm_e)*math.cos(psi-(math.pi/2-angle_m3))
		zp = -self.arm_c*math.cos(angle_m3) - (self.arm_d+self.arm_e)*math.sin(psi-(math.pi/2-angle_m3))
		z = zp*math.cos(angle_m1)
		y = -zp*math.sin(angle_m1)
		# print(x)
		# print(y)
		# print(z)

		return np.array([x, y, z])

	def leg_angle_grad(self, angle):
		shift = 1e-8

		angle_m1 = angle[0]
		angle_m2 = angle[1]
		angle_m3 = angle[2]

		m1_plus = self.leg_rad2pos([angle_m1 + shift, angle_m2, angle_m3])
		m1_minus = self.leg_rad2pos([angle_m1 - shift, angle_m2, angle_m3])
		m1_grad = (0.5 * (m1_plus - m1_minus))/shift

		m2_plus = self.leg_rad2pos([angle_m1, angle_m2 + shift, angle_m3])
		m2_minus = self.leg_rad2pos([angle_m1, angle_m2 - shift, angle_m3])
		m2_grad = (0.5 * (m2_plus - m2_minus))/shift

		m3_plus = self.leg_rad2pos([angle_m1, angle_m2, angle_m3 + shift])
		m3_minus = self.leg_rad2pos([angle_m1, angle_m2, angle_m3 - shift])
		m3_grad = (0.5 * (m3_plus - m3_minus))/shift

		# print(m1_grad)
		# print(m2_grad)
		# print(m3_grad)

		jacobian = np.matrix([m1_grad, m2_grad, m3_grad])
		# print(jacobian)

		return jacobian

	def leg_omega2velocity(self, angle, omega):
		jacobian = self.leg_angle_grad(angle)
		velocity = omega*jacobian
		return velocity


	def leg_status_update(self, angle, omega):
		self.angle = angle
		self.omega = omega
		self.pos = leg_rad2pos(angle)
		self.vel = leg_vel2omega(angle, omega)

	def boundary(self):
		pass
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

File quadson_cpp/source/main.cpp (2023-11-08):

#include "AHRS.hpp"
#include "can_interface.h"
#include "quadson.h"
#include <Common/Util.h>
#include <stdio.h>
#include <string.h>
#include <unistd.h>
#include <can_protocol.h>

int main() {
  if (check_apm()) { // check Navio sensor is not running
    return 1;
  }

  //--------------------------- Network setup -------------------------------

  Can_interface can_dev;
  AHRS ahrs;
  Quadson quadson(&can_dev);

  quadson.scan();
  // sleep(1);
  //-------------------- Setup gyroscope offset -----------------------------

  // ahrs.setGyroOffset();

  //------------------------ Read Euler angles ------------------------------
  // Orientation data

  // -------- Read raw measurements from the MPU and update AHRS --------------
  // float roll, pitch, yaw;

  // ahrs.getEuler(&roll, &pitch, &yaw);
  // while (1) {
  //   ahrs.update();
  //   quadson.update();
  //   sleep(0.5);
  // }

  // -------------------- Testing section -----------------------------------
  quadson.moving_test();
  
  can_dev.can_close();
  return 0;
}

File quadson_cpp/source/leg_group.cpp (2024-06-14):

#include "leg_group.h"

Eigen::Vector3f leg_rad2pos(Eigen::Vector3f angle);
Eigen::Vector3f leg_pos2rad(Eigen::Vector3f position);
Eigen::Matrix3f leg_pos_grad(Eigen::Vector3f position);
Eigen::Matrix3f leg_angle_grad(Eigen::Vector3f angle);

Leg_group::Leg_group() {}
Leg_group::Leg_group(Actuator *motorAlpha, Actuator *motorBeta,
                     Actuator *motorGamma) {
  this->mMotorAlpha = motorAlpha;
  this->mMotorBeta = motorBeta;
  this->mMotorGamma = motorGamma;

  pos.Zero();
  vel.Zero();
  ang.Zero();
  omg.Zero();

  ang_kp = ANG_KP;
  ang_ki = ANG_KI;
  ang_kd = ANG_KD;

  prev_ang_time = 0;
  prev_ang_error = 0;
  ang_error_integral = 0;
}

Leg_group::~Leg_group() {}

Eigen::Vector3f leg_pos2rad(Eigen::Vector3f position) {
  float x = position(0);
  float y = position(1);
  float z = position(2);

  float angle_m1 = atan2(y, -z);
  float r_m3 = CALC_R((MOTOR_DISTANCE - x), -CALC_R(y, z));
  float theta_m3 = atan2((MOTOR_DISTANCE - x), CALC_R(y, z));
  float psi_m3 = acos((pow((ARM_D + ARM_E), 2) - pow(ARM_C, 2) - pow(r_m3, 2)) /
                      (-2 * ARM_C * r_m3));
  float angle_m3 = psi_m3 - theta_m3;
  float beta_m3 =
      acos((pow(r_m3, 2) - pow((ARM_D + ARM_E), 2) - pow(ARM_C, 2)) /
           (-2 * ARM_C * (ARM_D + ARM_E)));
  float r_m3p =
      sqrt(pow(ARM_C, 2) + pow(ARM_D, 2) - 2 * ARM_C * ARM_D * cos(beta_m3));
  float psi_m3p = acos((pow(ARM_D, 2) - pow(ARM_C, 2) - pow(r_m3p, 2)) /
                       (-2 * ARM_C * r_m3p));
  float theta_m3p = psi_m3p - angle_m3;
  float r_m2 = CALC_R((MOTOR_DISTANCE - r_m3p * sin(theta_m3p)),
                      -r_m3p * cos(theta_m3p));
  float psi_m2 = acos((pow(ARM_B, 2) - pow(ARM_A, 2) - pow(r_m2, 2)) /
                      (-2 * ARM_A * r_m2));
  float theta_m2 =
      atan2((MOTOR_DISTANCE - r_m3p * sin(theta_m3p)), r_m3p * cos(theta_m3p));
  float angle_m2 = psi_m2 - theta_m2;

#ifdef DEBUG_LEGGROUP
  // # print(degrees(angle_m1))
  // # print(degrees(angle_m2))
  // # print(degrees(angle_m3))
#endif
  return Eigen::Vector3f(angle_m1, angle_m2, angle_m3);
}

Eigen::Vector3f leg_rad2pos(Eigen::Vector3f angle) {
  float angle_m1 = angle(0);
  float angle_m2 = angle(1);
  float angle_m3 = angle(2);

  double f = sqrt(pow(ARM_A, 2) + pow(MOTOR_DISTANCE, 2) -
                  2 * ARM_A * MOTOR_DISTANCE * cos(angle_m2 + M_PI / 2));

  float g =
      CALC_R(-ARM_A * sin(angle_m2) - (MOTOR_DISTANCE + ARM_C * sin(angle_m3)),
             -ARM_A * cos(angle_m2) - (-ARM_C * cos(angle_m3)));
  float psi = acos((pow(f, 2) - pow(ARM_C, 2) - pow(g, 2)) / (-2 * ARM_C * g));
  float psi_1 =
      acos((pow(ARM_B, 2) - pow(ARM_D, 2) - pow(g, 2)) / (-2 * ARM_D * g));
  psi = psi + psi_1;

  float x = MOTOR_DISTANCE + ARM_C * sin(angle_m3) -
            (ARM_D + ARM_E) * cos(psi - (M_PI / 2 - angle_m3));
  float zp = -ARM_C * cos(angle_m3) -
             (ARM_D + ARM_E) * sin(psi - (M_PI / 2 - angle_m3));
  float z = zp * cos(angle_m1);
  float y = -zp * sin(angle_m1);

#ifdef DEBUG_LEGGROUP
#print(x)
#print(y)
#print(z)
#endif
  return Eigen::Vector3f(x, y, z);
}

Eigen::Matrix3f leg_pos_grad(Eigen::Vector3f position) {
  double shift = 1e-8;

  float x = position[0];
  float y = position[1];
  float z = position[2];

  Eigen::Vector3f x_plus = leg_pos2rad(Eigen::Vector3f(x + shift, y, z));
  Eigen::Vector3f x_minus = leg_pos2rad(Eigen::Vector3f(x - shift, y, z));
  Eigen::Vector3f x_grad = (0.5 * (x_plus - x_minus)) / shift;

  Eigen::Vector3f y_plus = leg_pos2rad(Eigen::Vector3f(x, y + shift, z));
  Eigen::Vector3f y_minus = leg_pos2rad(Eigen::Vector3f(x, y - shift, z));
  Eigen::Vector3f y_grad = (0.5 * (y_plus - y_minus)) / shift;

  Eigen::Vector3f z_plus = leg_pos2rad(Eigen::Vector3f(x, y, z + shift));
  Eigen::Vector3f z_minus = leg_pos2rad(Eigen::Vector3f(x, y, z - shift));
  Eigen::Vector3f z_grad = (0.5 * (z_plus - z_minus)) / shift;

  Eigen::Matrix3f jacobian;
  jacobian << x_grad, y_grad, z_grad;
#ifdef DEBUG_LEGGROUP
#print(x_grad)
#print(y_grad)
#print(z_grad)
#print(jacobian)
#endif
  return jacobian;
}

Eigen::Matrix3f leg_angle_grad(Eigen::Vector3f angle) {
  double shift = 1e-8;

  float angle_m1 = angle[0];
  float angle_m2 = angle[1];
  float angle_m3 = angle[2];

  Eigen::Vector3f m1_plus =
      leg_rad2pos(Eigen::Vector3f(angle_m1 + shift, angle_m2, angle_m3));
  Eigen::Vector3f m1_minus =
      leg_rad2pos(Eigen::Vector3f(angle_m1 - shift, angle_m2, angle_m3));
  Eigen::Vector3f m1_grad = (0.5 * (m1_plus - m1_minus)) / shift;

  Eigen::Vector3f m2_plus =
      leg_rad2pos(Eigen::Vector3f(angle_m1, angle_m2 + shift, angle_m3));
  Eigen::Vector3f m2_minus =
      leg_rad2pos(Eigen::Vector3f(angle_m1, angle_m2 - shift, angle_m3));
  Eigen::Vector3f m2_grad = (0.5 * (m2_plus - m2_minus)) / shift;

  Eigen::Vector3f m3_plus =
      leg_rad2pos(Eigen::Vector3f(angle_m1, angle_m2, angle_m3 + shift));
  Eigen::Vector3f m3_minus =
      leg_rad2pos(Eigen::Vector3f(angle_m1, angle_m2, angle_m3 - shift));
  Eigen::Vector3f m3_grad = (0.5 * (m3_plus - m3_minus)) / shift;

  Eigen::Matrix3f jacobian;
  jacobian << m1_grad, m2_grad, m3_grad;
#ifdef DEBUG_LEGGROUP
#print(m1_grad)
#print(m2_grad)
#print(m3_grad)
#print(jacobian)
#endif
  return jacobian;
}

void matrixTest() {
  Eigen::Vector3f x_grad(0, 0, 0);
  Eigen::Vector3f y_grad(1, 0, 0);
  Eigen::Vector3f z_grad(0, 3, 0);
  Eigen::Matrix3f jacobian;
  jacobian << x_grad, y_grad, z_grad;
  std::cout << jacobian;
}

// For 2D test
Leg_group::Leg_group(Actuator *motorAlpha, Actuator *motorBeta) {
  mMotorAlpha = motorAlpha;
  mMotorBeta = motorBeta;
}

void Leg_group::leg_enable_torque(int num){
  this->mMotorAlpha->torque_enable(num); 
  this->mMotorBeta->torque_enable(num);
  // this->mMotorGamma->torque_enable(num);
}

bool Leg_group::leg_reset_pos() {
  if( !(mMotorAlpha->isZeroed() and mMotorBeta->isZeroed()) ) {
    this->mMotorAlpha->control_mode(1);
    this->mMotorBeta->control_mode(1);
    this->mMotorAlpha->goal_velocity_dps(50);
    this->mMotorBeta->goal_velocity_dps(50);
    this->mMotorAlpha->check_zero_done();
    this->mMotorBeta->check_zero_done();
    return true; 
  } else {
    this->mMotorAlpha->goal_velocity_dps(0);
    this->mMotorBeta->goal_velocity_dps(0);
    this->mMotorAlpha->control_mode(0);
    this->mMotorBeta->control_mode(0);
    return false; // if complete reseting, break from reset while.
  }
}
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

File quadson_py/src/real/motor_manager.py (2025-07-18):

import sys, os
sys.path.append(os.path.abspath(os.path.join(os.path.dirname(__file__), '../..')))

import struct
import threading
import time
import cando
import math
from src.real.can_config import *
from src.real.can_message import CanMessage
from src.real.motor import Motor

ID_STD_OFFSET = 6
ID_EXT_OFFSET = 24

class MotorManager:
	def __init__(self):
		self.dev_lists = None
		self.motor_list = [None] * 12

		# Create 12 motor objects
		for x in range(12):
			self.motor_list[x] = Motor(x, False)
		self.rec_frame = cando.Frame()

		self.connect_can_device()
		self.thread_pause_event = threading.Event()
		self.thread_stop_event = threading.Event()
		self.reading_thread = threading.Thread(target = self._can_read_handle)

		self.thread_stop_event.set()
		self.reading_thread.start()

		self._scan_motors()
		self._set_auto_receive(True)
	
	def connect_can_device(self):
		self.dev_lists = cando.list_scan()

		if len(self.dev_lists) == 0:
			print("Device not found!")
			sys.exit(0)

		if os.name == 'posix':  # for linux os
			if self.dev_lists[0].is_kernel_driver_active(0):
				self.dev_lists[0].detach_kernel_driver(0)

		# set baudrate: 500K, sample point: 87.5%
		cando.dev_set_timing(self.dev_lists[0], 1, 12, 6, 1, 6)

		cando.dev_start(self.dev_lists[0], cando.CANDO_MODE_NORMAL | cando.CANDO_MODE_NO_ECHO_BACK)

	def disconnect_can_device(self):
		self.thread_stop_event.clear()
		cando.dev_stop(self.dev_lists[0])
	
	def send_motor_cmd(self, motor_index, cmd, value):
		if self.motor_list[motor_index-1].exist == False:
			print("Motor unconnected")
			return

		send_frame = cando.Frame()
		
		if (cmd.__class__) == CAN_STD_TYPE:
			send_frame.can_id = 0x00 | (motor_index << ID_STD_OFFSET) | cmd.value
		else:
			send_frame.can_id = 0x00 | (motor_index << ID_EXT_OFFSET) | cmd.value
			send_frame.can_id |= cando.CANDO_ID_EXTENDED

		send_frame.can_dlc = 2
		send_frame.data = [value >> 8, value & 0xFF, 0x00, 0x00, 0x00, 0x00, 0x00, 0x00]
		cando.dev_frame_send(self.dev_lists[0], send_frame)
		# print("sending message id:" + str(send_frame.can_id))
		
	def get_angle(self, motor_id):
		self.send_motor_cmd(motor_id, CAN_STD_TYPE.CAN_STDID_PRESENT_REVOLUTION, 0)
		self.send_motor_cmd(motor_id, CAN_STD_TYPE.CAN_STDID_PRESENT_POSITION_DEG, 0)
		
		revolution = self.motor_list[motor_id-1].get_param(CMD_TYPE.PRESENT_REVOLUTION)
		angle_16 = self.motor_list[motor_id-1].get_param(CMD_TYPE.PRESENT_POSITION_DEG)
		# print("rev: " + str(revolution) + "  angle: " + str(angle_16))

		angle = (revolution + ( (angle_16) / 65536))/71.96 * 2*math.pi
		# print("degree: " + str(math.degrees(angle)))
		
		return angle

	def set_angle(self, motor_id, angle):
		pass

	def get_omega(self, motor_id):
		self.send_motor_cmd(motor_id, CAN_STD_TYPE.CAN_STDID_PRESENT_VELOCITY_DPS, 0)
		velocity_01 = self.motor_list[motor_id-1].get_param(CMD_TYPE.PRESENT_VELOCITY_DPS)

		omega = (((velocity_01*10) / 65536))/71.96 * 2*math.pi
		# print("omega: " + str(omega))
		return omega
	
	def set_omega(self, motor_id, omega):
		pass

	def _can_read_handle(self):
		while self.thread_stop_event.isSet():
			self.thread_pause_event.wait()
			if cando.dev_frame_read(self.dev_lists[0], self.rec_frame, 1):
				if (not self._msg_error(self.rec_frame)):
					self._decode_msg(self.rec_frame)
				else:
					print("reading error")
					self.disconnect_can_device()
	
	def _scan_motors(self):
		print("Scaning...")
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

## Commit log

2024-04-27 Add simuilation model files
    [Empty_Link.STL, FR_1_link.STL, FR_2_link.STL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]
2024-06-14 Add new files and make changes to existing files
    [Empty_Link.STL, FR_1_link.STL, FR_2_link.STL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]
2024-12-20 Update enviroment build
    [base_link.STL, fr_link_0.STL, fr_link_1.STL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]
2025-02-18 Update differential kinematics
2025-02-19 Update kinematics in R3
2025-02-20 Update kinematics calculations in R^3
2025-02-20 Update Differential forward kinematics
2025-02-20 Update differential inverse kinematics
2025-02-23 Update kinematics algorithms
2025-02-24 Update body kinematics
2025-02-25 Update bodty inverse kinematic
2025-02-25 Add leg class
2025-02-26 Update body kinematic
2025-02-28 Add plane mesh and simulation loading script
    [base_link.STL, fr_link_0.STL, fr_link_1.STL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]
2025-02-28 Update simulation loading script and URDF file for quadson robot
    [quadson.urdf]
2025-02-28 Enable collision object in simulation
    [quadson.urdf, quadson_modified.urdf]
2025-03-01 Update file structure
    [base_link.STL, base_link.stl, bl_link0.stl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]
2025-03-01 Update mesh
    [quadson.urdf]
2025-03-11 Update folder names
    [base_link.STL, base_link.stl, bl_link0.stl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]
2025-03-12 Update urdf script
2025-03-12 Add single leg test
    [link - low_arm_rear-3.stl, link - touch_part-2.stl, link - up_arm-5.001.stl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]
2025-03-12 Add quadson whole body test
    [base_link.STL, base_link.stl, bl_link0.stl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]
2025-03-13 Fix the warning of lacking inertia
    [quadson_modified.urdf]
2025-03-13 Update body and leg kinematics
2025-03-18 Refactor simulation setup and introduce actuator class for motor control
2025-03-24 Update single leg, achieve closed chain
    [link - low_arm_rear-3.stl, link - touch_part-2.stl, link - up_arm-5.001.stl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]
2025-03-25 Update single leg test
2025-03-25 Enable slider control whole body joint
    [fl_link3.stl, fl_link4.stl, fl_link5.stl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]
2025-03-26 Remove the calculation of alternative point in inverse kinematics
2025-03-26 Refactor Quadson class to integrate Interface and BodyKinematics, removing slider interface and updating motor and orientation handling methods.
2025-04-08 Rename folder
    [base_link.stl, fl_link0.stl, fl_link1.stl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]
